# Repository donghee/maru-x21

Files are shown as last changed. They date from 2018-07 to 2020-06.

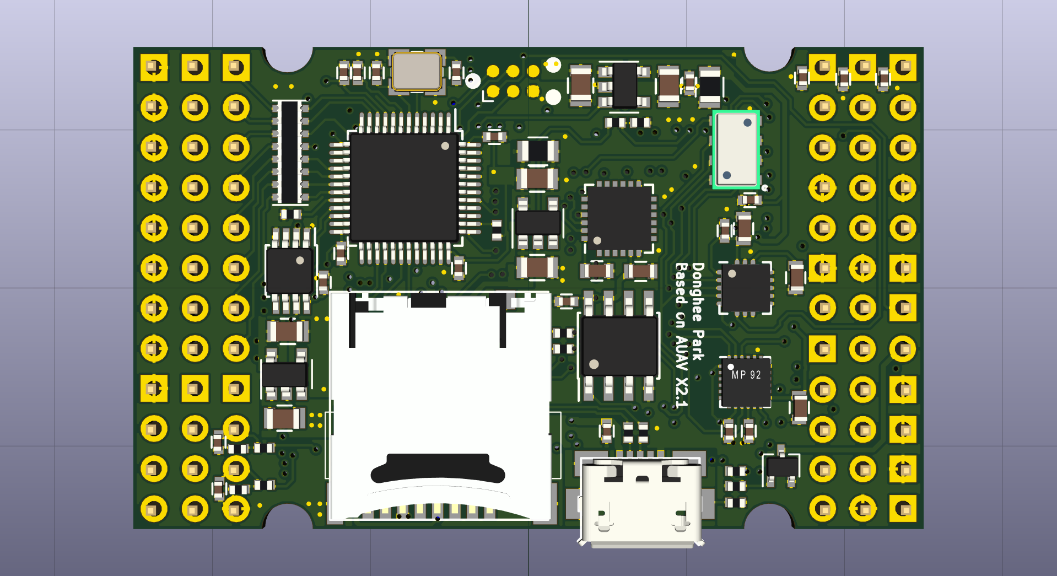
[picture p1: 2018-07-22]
maru-x21_3d_back.png

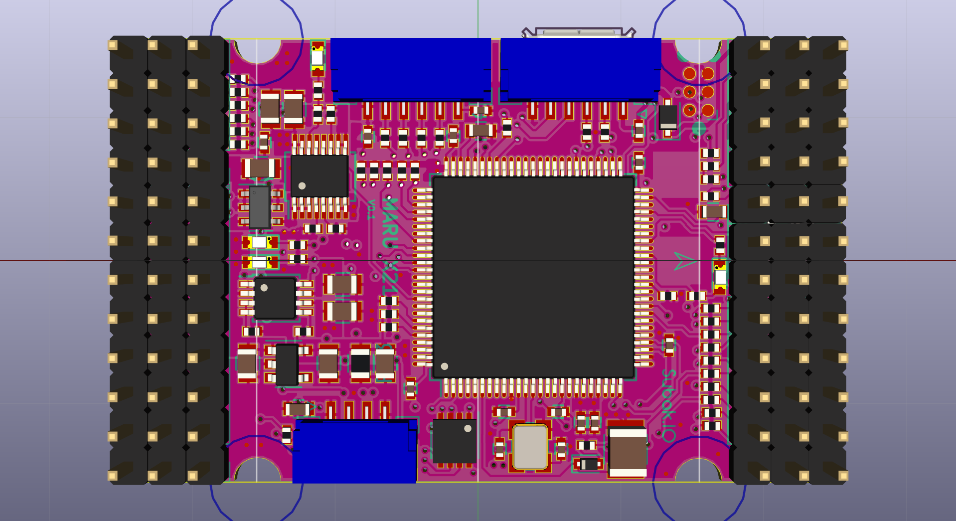
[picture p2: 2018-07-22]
maru-x21_3d_front.png

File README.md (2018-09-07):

# MARU X21

Pixhawk compatible autopilot based from AUAV X2.1

PCB assembly and program bootloader

PCB assembly (https://youtu.be/ogCYYdSt7_Y?t=0)

Case assembly

Case assembly (https://youtu.be/GHVFkq7RcLQ?t=0)

Maiden flight

Maiden flight (https://youtu.be/oDkj_PMFI5Y?t=0)

----

# Secification

FMU processor: stm32f427vit6
 - 32-bit ARM Cortex M4 core with FPU
 - 180 Mhz/256 KB RAM/2 MB Flash

IO processor: stm32f100c8t6
 - 32-bit ARM Cortex M3 core
 - 24 MHz/8 KB RAM/64 KB Flash

IMU sensors
 - icm-20602 6 axis accel and gyro (main imu)
 - mpu-9250 9 axis accel and gyro and mag
 - ms5611 barometer

Interfaces
 - 5x UARTs
 - 1x CANbus
 - RC Interfaces: PPM/SBUS/DSM/RSSI Input
 - I2C
 - SPI

Power Input
 - 4.8v~5.4v

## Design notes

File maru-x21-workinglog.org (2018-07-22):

* 사전조사

CUAV_Hardware

 - https://github.com/cuav/CUAV_Hardware/tree/master/6S_Smart%20batt-DEMO
 - https://github.com/cuav/CUAV_Hardware/tree/master/Pixhack_V3

Dropix

 - https://github.com/drotek/Dropix/blob/master/Hardware/Dropix.PDF

* Project Log

** <2017-12-31 일>
아침에 일어 났다. 'The Deveil is a Part-Timer'를 켜두고 pixracer
참고하는중. 

2017-12-31-13:58
목이 좀 아프네. 오늘의 목표 maru-pixracer-power 완성 

** <2018-02-04 일>

maru-pixracer 파워 패스 

PX4FMUv2 픽스호크는 servo 로부터 파워를 받는데 
X21_V2는 servo로 부터 파워를 받지 않는다. 
기본 파워는 VBUS(USB)와 V_BRICK(파워모듈)로 부터 받고 
LTC4415 (파워OR, 전류제한) 를 거쳐서 VDD_5V를 만든다. 
VDD_5V는 4개의 LDO(LP5907-Q1, 250mA)을 거쳐서 각각 
내부 파워 (IO_VDD_3V3, FMU_VDD_3V3, VDD_3V3_SPEKTRUM, VDD_3V3_SENSORS)로 출력되고 
VDD_5V는 TPS2062(1A Dual Current Limiter, 파워 스위치) 외부 파워에 나눌때는 TPS2062사용 를 거쳐 두개의 외부 파워 (VDD_5V_PERIPH, VDD_5V_RC)로 출력된다. 

** <2018-02-17 토>
 - [ ] schematic 그리기 작업 
201~200~FTSH-103-02-L-DV

** <2018-02-19 월>
maru 작업 순서 

 - 0. schematic 그리기
 - 1. schematic 검토 *
 - 2. part package 매칭
 - 3. pcb 그리기 
 - 4. 부품구매 
 - 5. 조립 
 - 6. 테스트/펌웨어 올리기

** <2018-02-21 화>
20mmx20mm 원점 잡고. maru x21 PCB 그리는중. 50x30.5 사이즈.

Dwgs.User에 가이드선 그리고 그리니깐 편리하네 

** <2018-02-22 Thu>

 - 3. pcb 그리기 작업중

FTSH-103-02-L-DV

** <2018-03-13 화>
 - 4층 각층은 동박은 1 ounce 두께로 주문 
 - 외곽선이 3지점 라인을 손상 시킨다. 한샘디지텍 외곽선 0.2 공차오차가
   있다. 그래서 좌우 0.5mm씩 늘려버리기로.
 주문한 메탈마스크 업체: 2장에 10만원 
 - 덕진전자 현수 010-5345-7023 dreammer70@hanmail.net
    경기도 광명시 광명로831번길 9, 3층 

** <2018-04-01 일>
 - 납땜 필요.
 -

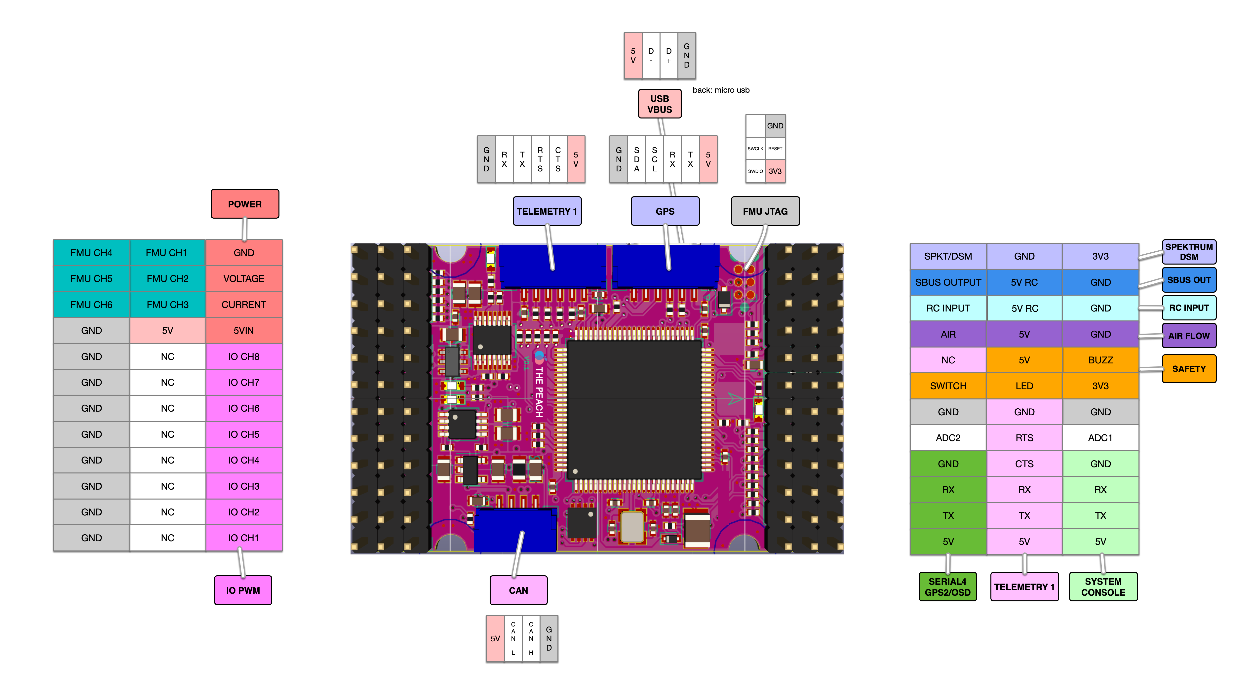
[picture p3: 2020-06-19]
doc/maru-x21-v01_legend.png

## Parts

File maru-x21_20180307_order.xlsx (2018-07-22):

C1-C7,C11,C20,C21,C28,C30-C36,C38-C41,C43,C49,C51,C52,C54,C57-C61 | 100nF | Capacitors_SMD:C_0402_NoSilk | GCM155R71C104KA55D | 32 | 45.4 | 1452.8 | 326637 | 45.4 | 1452.8 | 490-4759-1-ND
C10 | 220uF | Capacitors_SMD:C_1210 | CL32A227MQVNNNE | 1 | 1677 | 1677 | 309785 | 1677 | 1677 | 1276-3375-1-ND
C12,C13,C42,C48,C50 | 2u2F | Capacitors_SMD:C_0603 | C1608X5R1C225K080AB | 5 | 244 | 1220 | 302411 | 244 | 1220 | 445-5157-1-ND
C14-C17 | 2u2F 10V | Capacitors_SMD:C_0805 | C2012X5R1A225K085AA | 4 | 233 | 932 | 28286 | 233 | 932 | 445-1588-1-ND
C18,C19,C44,C45 | 8pF | Capacitors_SMD:C_0402_NoSilk | GRM1555C1E8R0CA01D | 4 | 116 | 464 | 48515 | 116 | 464 | 490-11372-1-ND
C22-C26 | 10uF 10V | Capacitors_SMD:C_0805 | C2012X5R1A106K085AB | 5 | 338 | 1690 | 142606 | 338 | 1690 | 445-7658-1-ND
C27,C29,C47 | 1uF | Capacitors_SMD:C_0603 | C1608X5R1C105K080AA | 3 | 116 | 348 | 17962 | 116 | 348 | 445-1416-1-ND
C46 | 470nF | Capacitors_SMD:C_0603 | GRM188R71C474KA88D | 1 | 198 | 198 | 459793 | 198 | 198 | 490-3295-1-ND
C53 | 10uF 16V | Capacitors_SMD:C_0805 | C2012X5R1C106K085AC | 1 | 303 | 303 | 57768 | 303 | 303 | 445-7644-1-ND
C55#2,C56#2 | 47uF 16V - p2/2 | Capacitors_SMD:C_0805 | LMK212BBJ476MG-T | 2 | 1106 | 2212 | 282 | 1106 | 2212 | 587-5465-1-ND
C8,C9 | 10uF 16V | Capacitors_SMD:C_0805 | C3216X5R1C106K160AA | 2 | 314 | 628 | 162965 | 314 | 628 | 445-4052-1-ND
D2#2 | BAS70-02V - p2/2 | Diodes_SMD:D_SOD-523 | BAS70KFILM | 1 | 303 | 303 | 31366 | 303 | 303 | 497-5695-1-ND
D6 | 1N4148WT | Diodes_SMD:D_SOD-523 | 1N4148WT | 1 | 233 | 233 | 243571 | 233 | 233 | 1N4148WTCT-ND
D7#1 | PMEG3002 - p1/2 | Diodes_SMD:D_SOD-323F | PMEG3002EJ | 1 | 594 | 594 | 74070 | 594 | 594 | 1727-5828-1-ND
J17 | SERIAL1 | Connectors_JST:JST_GH_SM06B-GHS-TB_06x1.25mm_Angled | SM06B-GHS-TB(LF)(SN) | 1 | 675 | 675 | 26740 | 675 | 675 | 455-1568-1-ND
J19 | CAN | Connectors_JST:JST_GH_SM04B-GHS-TB_04x1.25mm_Angled | SM04B-GHS-TB(LF)(SN)- | 1 | 524 | 524 | 84179 | 524 | 524 | 455-1566-1-ND
J22 | GPS/I2C | Connectors_JST:JST_GH_SM06B-GHS-TB_06x1.25mm_Angled | SM06B-GHS-TB(LF)(SN) | 1 | 675 | 675 | 26740 | 675 | 675 | 455-1568-1-ND
J4 | Micro_SD_Card | swi_sdcard:DM3CS-SF | DM3CS-SF | 1 | 1758 | 1758 | 20163 | 1758 | 1758 | HR1972CT-ND
P1 | USB_OTG | pkl_connectors:Connector_USB_Micro_B_SMD | 10118192-0001LF | 1 | 536 | 536 | 167623 | 536 | 536 | 609-4613-1-ND
Q1 | SI3493BDV | Housings_SSOP:TSOP-6_1.65x3.05mm_Pitch0.95mm | SI3493BDV-T1-E3 | 1 | 1013 | 1013 | 2716 | 1013 | 1013 | SI3493BDV-T1-E3CT-ND
Q2 | DMG1012UW | TO_SOT_Packages_SMD:SOT-323_SC-70 | DMG1012UW-7 | 1 | 454 | 454 | NonStk | 454 | 454 | DMG1012UW-7DICT-ND | element14
R1,R4,R34,R35,R38 | 470 | Resistors_SMD:R_0402_NoSilk | ERJ-2GEJ471X | 5 | 116 | 580 | 731945 | 116 | 580 | P470JCT-ND
R10,R11 | 470K | Resistors_SMD:R_0402_NoSilk | ERJ-2GEJ474X | 2 | 116 | 232 | 1980943 | 116 | 232 | P470KJCT-ND
R15,R29,R30 | 1K | Resistors_SMD:R_0402_NoSilk | ERJ-2GEJ102X | 3 | 116 | 348 | 969065 | 116 | 348 | P1.0KJCT-ND
R2,R8,R9,R12-R14,R33,R45,R46,R48-R52,R64 | 10K | Resistors_SMD:R_0402_NoSilk | RC1005J103CS | 15 | 14 | 210 | 317110 | 14 | 210 | 1276-4400-1-ND
R22,R23 | 220 | Resistors_SMD:R_0805 | RC2012J221CS | 2 | 116 | 232 | 91887 | 116 | 232 | 1276-5515-1-ND
R24 | 2K7 | Resistors_SMD:R_0402_NoSilk | ERJ-2GEJ272X | 1 | 116 | 116 | 351274 | 116 | 116 | P2.7KJCT-ND
R25,R26 | 1M | Resistors_SMD:R_0402_NoSilk | ERJ-2GEJ105X | 2 | 116 | 232 | 22059 | 116 | 232 | P1.0MJCT-ND
R27,R28 | 22 | Resistors_SMD:R_0402_NoSilk | ERJ-2GEJ220X | 2 | 116 | 232 | 3194228 | 116 | 232 | P22JCT-ND
R3,R7,R16-R20 | 100K | Resistors_SMD:R_0402_NoSilk | ERJ-2GEJ104X | 7 | 116 | 812 | 499925 | 116 | 812 | P100KJCT-ND
R31,R32,R39-R44,R53-R61,R65,R68-R73 | 220 | Resistors_SMD:R_0402_NoSilk | ERJ-2GEJ221X | 24 | 33.8 | 811.2 | 1861532 | 33.8 | 811.2 | P220JCT-ND
R36 | 47 | Resistors_SMD:R_0402_NoSilk | ERJ-2GEJ470X | 1 | 116 | 116 | 836865 | 116 | 116 | P47JCT-ND
R37,R66,R67 | 1K5 | Resistors_SMD:R_0402_NoSilk | ERJ-2GEJ152X | 3 | 116 | 348 | 1635661 | 116 | 348 | P1.5KJCT-ND
R47 | 10 | Resistors_SMD:R_0402_NoSilk | ERJ-2GEJ100X | 1 | 116 | 116 | 4075179 | 116 | 116 | P10JCT-ND
R5 | 200 1% | Resistors_SMD:R_0402_NoSilk | ERJ-2RKF2000X | 1 | 116 | 116 | 1402 | 116 | 116 | P200LCT-ND
R6 | 1K 1% | Resistors_SMD:R_0402_NoSilk | ERJ-2RKF1001X | 1 | 116 | 116 | 1120821 | 116 | 116 | P1.00KLCT-ND
R62 | 100 | Resistors_SMD:R_0402_NoSilk | ERJ-2GEJ101X | 1 | 116 | 116 | 1670945 | 116 | 116 | P100JCT-ND
R63 | 120 | Resistors_SMD:R_0402_NoSilk | ERJ-2GEJ121X | 1 | 116 | 116 | 624665 | 116 | 116 | P120JCT-ND
RN1 | 220 | Resistors_SMD:R_Cat16-8 | CAT16-221J8LF | 1 | 466 | 466 | 7585 | 466 | 466 | CAT16-221J8LFCT-ND
U1 | LTC4415 | Housings_SSOP:MSOP-16-1EP_3x4mm_Pitch0.5mm | LTC4415EMSE#PBF | 1 | 7463 | 7463 | 4642 | 7463 | 7463 | LTC4415EMSE#PBF-ND
U10 | MS5611-01BA03 | swi_sensors:ms5611-01ba03 | MS561101BA03-50 | 1 | 14530 | 14530 | NonStk | 14530 | 14530 | 223-1622-1-ND | element14
U11 | STM32F100C8T6 | Housings_QFP:LQFP-48_7x7mm_Pitch0.5mm | STM32F100C8T6B | 1 | 3854 | 3854 | 7195 | 3854 | 3854 | 497-10499-ND
U12 | ICM-20602 | swi_sensors:LGA-16_3x3mm_Pitch0.5mm | ICM-20602 | 1 | 6659 | 6659 | 17223 | 6659 | 6659 | 1428-1060-1-ND
U13#1 | TJA1051TK/3 - p1/2 | Housings_DFN_QFN:DFN-8-1EP_3x3mm_Pitch0.65mm | TJA1051TK/3 | 1 | 1234 | 1234 | 115301 | 1234 | 1234 | 568-8686-1-ND
U14#1 | 74LVC2G240 - p1/2 | Housings_SSOP:TSSOP-8_3x3mm_Pitch0.65mm | 74LVC2G240DP | 1 | 629 | 629 | 14869 | 629 | 629 | 1727-6678-1-ND
U15 | MPU-9250 | swi_sensors:QFN-24_3x3mm_Pitch0.4mm_large_pads | MPU-9250 | 1 | 12376 | 12376 | 56900 | 12376 | 12376 | 1428-1019-1-ND
U2 | TPS2062 | Housings_SSOP:MSOP-8-1EP_3x3mm_Pitch0.65mm | TPS2062CDGNR | 1 | 2177 | 2177 | 1345 | 2177 | 2177 | 296-41720-1-ND
U3 | STM32F427VIT6 | Housings_QFP:LQFP-100_14x14mm_Pitch0.5mm | STM32F427VIT6 | 1 | 16707 | 16707 | NonStk | 16707 | 16707 | 497-14049-ND | element14
U4-U7 | LP5907 | TO_SOT_Packages_SMD:SOT-23-5 | LP5907QMFX-3.3Q1 | 4 | 757 | 3028 | 21427 | 757 | 3028 | 296-40365-1-ND
U8 | FM25V02A-G | Housings_SOIC:SOIC-8_3.9x4.9mm_Pitch1.27mm | FM25V02A-G | 1 | 8150 | 8150 | 9435 | 8150 | 8150 | 428-3386-ND
X1,X2 | 24MHz | swi_misc:ABM8 | NX3225SA-24.000MHZ-STD-CSR-1 | 2 | 873 | 1746 | 49910 | 873 | 1746 | 644-1052-1-ND
부품종류
51 | 가지

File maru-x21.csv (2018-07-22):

Source: | /Users/donghee/Dropbox/dev/electrical/kicad/maru/maru-pixracer/maru-pixracer.sch
Date: | 2018 March 14, Wednesday 18:42:59
Tool: | Eeschema 4.0.7
Generator: | /Applications/Kicad/kicad.app/Contents/SharedSupport/plugins/bom_csv_grouped_by_value.py
Component Count: | 188
Individual Components:
Item | Qty | Reference(s) | Value | LibPart | Footprint | Datasheet | #mouser | digikey# | manf#
 |  | C1 | 100nF | maru-pixracer-cache:C_Small | swi_dipol:C_0402 |  |  |  | GCM155R71C104KA55D
 |  | C2 | 100nF | maru-pixracer-cache:C_Small | swi_dipol:C_0402 |  |  |  | GCM155R71C104KA55D
 |  | C3 | 100nF | maru-pixracer-cache:C_Small | swi_dipol:C_0402 |  |  |  | GCM155R71C104KA55D
 |  | C4 | 100nF | maru-pixracer-cache:C_Small | swi_dipol:C_0402 |  |  |  | GCM155R71C104KA55D
 |  | C5 | 100nF | maru-pixracer-cache:C_Small | swi_dipol:C_0402 |  |  |  | GCM155R71C104KA55D
 |  | C6 | 100nF | maru-pixracer-cache:C_Small | swi_dipol:C_0402 |  |  |  | GCM155R71C104KA55D
 |  | C7 | 100nF | maru-pixracer-cache:C_Small | swi_dipol:C_0402 |  |  |  | GCM155R71C104KA55D
 |  | C8 | 10uF 16V | maru-pixracer-cache:C_Small | swi_dipol:C_0805 |  |  |  | C3216X5R1C106K160AA
 |  | C9 | 10uF 16V | maru-pixracer-cache:C_Small | swi_dipol:C_0805 |  |  |  | C3216X5R1C106K160AA
 |  | C10 | 220uF | maru-pixracer-cache:C_Small | Capacitors_SMD:C_1210 |  |  |  | CL32A227MQVNNNE
 |  | C11 | 100nF | maru-pixracer-cache:C_Small | swi_dipol:C_0402 |  |  |  | GCM155R71C104KA55D
 |  | C12 | 2u2F | maru-pixracer-cache:C_Small | swi_dipol:C_0603 |  |  |  | C1608X5R1C225K080AB
 |  | C13 | 2u2F | maru-pixracer-cache:C_Small | swi_dipol:C_0603 |  |  |  | C1608X5R1C225K080AB
 |  | C14 | 2u2F 10V | maru-pixracer-cache:C_Small | swi_dipol:C_0805 |  |  |  | C2012X5R1A225K085AA
 |  | C15 | 2u2F 10V | maru-pixracer-cache:C_Small | swi_dipol:C_0805 |  |  |  | C2012X5R1A225K085AA
 |  | C16 | 2u2F 10V | maru-pixracer-cache:C_Small | swi_dipol:C_0805 |  |  |  | C2012X5R1A225K085AA
 |  | C17 | 2u2F 10V | maru-pixracer-cache:C_Small | swi_dipol:C_0805 |  |  |  | C2012X5R1A225K085AA
 |  | C18 | 8pF | maru-pixracer-cache:C_Small | swi_dipol:C_0402 |  |  |  | GRM1555C1E8R0CA01D
 |  | C19 | 8pF | maru-pixracer-cache:C_Small | swi_dipol:C_0402 |  |  |  | GRM1555C1E8R0CA01D
 |  | C20 | 100nF | maru-pixracer-cache:C_Small | swi_dipol:C_0402 |  |  |  | GCM155R71C104KA55D
 |  | C21 | 100nF | maru-pixracer-cache:C_Small | swi_dipol:C_0402 |  |  |  | GCM155R71C104KA55D
 |  | C22 | 10uF 10V | maru-pixracer-cache:C_Small | swi_dipol:C_0805 |  |  |  | C2012X5R1A106K085AB
 |  | C23 | 10uF 10V | maru-pixracer-cache:C_Small | swi_dipol:C_0805 |  |  |  | C2012X5R1A106K085AB
 |  | C24 | 10uF 10V | maru-pixracer-cache:C_Small | swi_dipol:C_0805 |  |  |  | C2012X5R1A106K085AB
 |  | C25 | 10uF 10V | maru-pixracer-cache:C_Small | swi_dipol:C_0805 |  |  |  | C2012X5R1A106K085AB
 |  | C26 | 10uF 10V | maru-pixracer-cache:C_Small | swi_dipol:C_0805 |  |  |  | C2012X5R1A106K085AB
 |  | C27 | 1uF | maru-pixracer-cache:C_Small | swi_dipol:C_0603 |  |  |  | C1608X5R1C105K080AA
 |  | C28 | 100nF | maru-pixracer-cache:C_Small | swi_dipol:C_0402 |  |  |  | GCM155R71C104KA55D
 |  | C29 | 1uF | maru-pixracer-cache:C_Small | swi_dipol:C_0603 |  |  |  | C1608X5R1C105K080AA
 |  | C30 | 100nF | maru-pixracer-cache:C_Small | swi_dipol:C_0402 |  |  |  | GCM155R71C104KA55D
 |  | C31 | 100nF | maru-pixracer-cache:C_Small | swi_dipol:C_0402 |  |  |  | GCM155R71C104KA55D
 |  | C32 | 100nF | maru-pixracer-cache:C_Small | swi_dipol:C_0402 |  |  |  | GCM155R71C104KA55D
 |  | C33 | 100nF | maru-pixracer-cache:C_Small | swi_dipol:C_0402 |  |  |  | GCM155R71C104KA55D
 |  | C34 | 100nF | maru-pixracer-cache:C_Small | swi_dipol:C_0402 |  |  |  | GCM155R71C104KA55D
 |  | C35 | 100nF | maru-pixracer-cache:C_Small | swi_dipol:C_0402 |  |  |  | GCM155R71C104KA55D
 |  | C36 | 100nF | maru-pixracer-cache:C_Small | swi_dipol:C_0402 |  |  |  | GCM155R71C104KA55D
 |  | C38 | 100nF | maru-pixracer-cache:C_Small | swi_dipol:C_0402 |  |  |  | GCM155R71C104KA55D
 |  | C39 | 100nF | maru-pixracer-cache:C_Small | swi_dipol:C_0402 |  |  |  | GCM155R71C104KA55D
 |  | C40 | 100nF | maru-pixracer-cache:C_Small | swi_dipol:C_0402 |  |  |  | GCM155R71C104KA55D
 |  | C41 | 100nF | maru-pixracer-cache:C_Small | swi_dipol:C_0402 |  |  |  | GCM155R71C104KA55D
 |  | C42 | 2u2F | maru-pixracer-cache:C_Small | swi_dipol:C_0603 |  |  |  | C1608X5R1C225K080AB
 |  | C43 | 100nF | maru-pixracer-cache:C_Small | swi_dipol:C_0402 |  |  |  | GCM155R71C104KA55D
 |  | C44 | 8pF | maru-pixracer-cache:C_Small | swi_dipol:C_0402 |  |  |  | GRM1555C1E8R0CA01D
 |  | C45 | 8pF | maru-pixracer-cache:C_Small | swi_dipol:C_0402 |  |  |  | GRM1555C1E8R0CA01D
 |  | C46 | 470nF | maru-pixracer-cache:C_Small | swi_dipol:C_0603 |  |  |  | GRM188R71C474KA88D
 |  | C47 | 1uF | maru-pixracer-cache:C_Small | swi_dipol:C_0603 |  |  |  | C1608X5R1C105K080AA
 |  | C48 | 2u2F | maru-pixracer-cache:C_Small | swi_dipol:C_0603 |  |  |  | C1608X5R1C225K080AB
 |  | C49 | 100nF | maru-pixracer-cache:C_Small | swi_dipol:C_0402 |  |  |  | GCM155R71C104KA55D
 |  | C50 | 2u2F | maru-pixracer-cache:C_Small | swi_dipol:C_0603 |  |  |  | C1608X5R1C225K080AB
 |  | C51 | 100nF | maru-pixracer-cache:C_Small | swi_dipol:C_0402 |  |  |  | GCM155R71C104KA55D
 |  | C52 | 100nF | maru-pixracer-cache:C_Small | swi_dipol:C_0402 |  |  |  | GCM155R71C104KA55D
 |  | C53 | 10uF 16V | maru-pixracer-cache:C_Small | swi_dipol:C_0805 |  |  |  | C2012X5R1C106K085AC
 |  | C54 | 100nF | maru-pixracer-cache:C_Small | swi_dipol:C_0402 |  |  |  | GCM155R71C104KA55D
 |  | C55 | 47uF 16V | maru-pixracer-cache:C_Small | swi_dipol:C_0805 |  |  |  | C2012X5R1A476M125AC, LMK212BBJ476MG-T
 |  | C56 | 47uF 16V | maru-pixracer-cache:C_Small | swi_dipol:C_0805 |  |  |  | C2012X5R1A476M125AC, LMK212BBJ476MG-T
 |  | C57 | 100nF | maru-pixracer-cache:C_Small | swi_dipol:C_0402 |  |  |  | GCM155R71C104KA55D
 |  | C58 | 100nF | maru-pixracer-cache:C_Small | swi_dipol:C_0402 |  |  |  | GCM155R71C104KA55D
 |  | C59 | 100nF | maru-pixracer-cache:C_Small | swi_dipol:C_0402 |  |  |  | GCM155R71C104KA55D
 |  | C60 | 100nF | maru-pixracer-cache:C_Small | swi_dipol:C_0402 |  |  |  | GCM155R71C104KA55D
 |  | C61 | 100nF | maru-pixracer-cache:C_Small | swi_dipol:C_0402 |  |  |  | GCM155R71C104KA55D
 |  | D1 | RED | maru-pixracer-cache:LED | LEDs:LED_0603
 |  | D2 | BAS70-02V | maru-pixracer-cache:D_Schottky | Diodes_SMD:D_SOD-523 |  |  |  | BAS70-02V-V-G-08, BAS70KFILM
 |  | D3 | GREEN | maru-pixracer-cache:LED | LEDs:LED_0603
 |  | D4 | RED | maru-pixracer-cache:LED | LEDs:LED_0603
 |  | D5 | BLUE | maru-pixracer-cache:LED | LEDs:LED_0603
 |  | D6 | 1N4148WT | maru-pixracer-cache:D_Schottky_Small | Diodes_SMD:D_SOD-523 |  |  |  | 1N4148WT
 |  | D7 | PMEG3002 | maru-pixracer-cache:D_Schottky | Diodes_SMD:D_SOD-323F |  |  |  | PMEG3002EJ,115
 |  | J1 | ARM Cortex JTAG 6p | maru-pixracer-cache:Conn_02x03_Odd_Even | swi_pads:Tag-Connect_TC2030-IDC-NL-NOHOLE
 |  | J2 | ARM Cortex JTAG 6p | maru-pixracer-cache:Conn_02x03_Odd_Even | swi_pads:Tag-Connect_TC2030-IDC-NL-NOHOLE
 |  | J3 | BRICK | maru-pixracer-cache:Conn_01x04 | Pin_Headers:Pin_Header_Straight_1x04_Pitch2.54mm
 |  | J4 | Micro_SD_Card | maru-pixracer-cache:Micro_SD_Card | swi_sdcard:DM3CS-SF |  |  |  | DM3CS-SF
 |  | J5 | IO_CHANNELS | maru-pixracer-cache:Conn_01x08 | Pin_Headers:Pin_Header_Straight_1x08_Pitch2.54mm
 |  | J6 | VDD_SERVO | maru-pixracer-cache:Conn_01x08 | Pin_Headers:Pin_Header_Straight_1x08_Pitch2.54mm
 |  | J7 | SERVO_GND | maru-pixracer-cache:Conn_01x08 | Pin_Headers:Pin_Header_Straight_1x08_Pitch2.54mm
 |  | J8 | SAFETY | maru-pixracer-cache:Conn_01x03 | Pin_Headers:Pin_Header_Straight_1x03_Pitch2.54mm
 |  | J9 | CH1-3 | maru-pixracer-cache:Conn_01x04 | Pin_Headers:Pin_Header_Straight_1x04_Pitch2.54mm
 |  | J10 | CH4-6 | maru-pixracer-cache:Conn_01x04 | Pin_Headers:Pin_Header_Straight_1x04_Pitch2.54mm
 |  | J11 | BUZZ | maru-pixracer-cache:Conn_01x03 | Pin_Headers:Pin_Header_Straight_1x03_Pitch2.54mm
 |  | J12 | AIR | maru-pixracer-cache:Conn_01x03 | Pin_Headers:Pin_Header_Straight_1x03_Pitch2.54mm
 |  | J13 | AUX-ADC1 | maru-pixracer-cache:Conn_01x02 | Pin_Headers:Pin_Header_Straight_1x02_Pitch2.54mm
 |  | J14 | AUX-ADC2 | maru-pixracer-cache:Conn_01x02 | Pin_Headers:Pin_Header_Straight_1x02_Pitch2.54mm
 |  | J15 | SIPI | maru-pixracer-cache:Conn_01x03 | Pin_Headers:Pin_Header_Straight_1x03_Pitch2.54mm
 |  | J16 | SPEKT | maru-pixracer-cache:Conn_01x03 | Pin_Headers:Pin_Header_Straight_1x03_Pitch2.54mm
 |  | J17 | SERIAL1 | maru-pixracer-cache:Conn_01x06 | Connectors_JST:JST_GH_SM06B-GHS-TB_06x1.25mm_Angled |  |  |  | SM06B-GHS-TB(LF)(SN)
 |  | J18 | TELEM2 | maru-pixracer-cache:Conn_01x06 | Pin_Headers:Pin_Header_Straight_1x06_Pitch2.54mm
 |  | J19 | CAN | maru-pixracer-cache:Conn_01x04 | Connectors_JST:JST_GH_SM04B-GHS-TB_04x1.25mm_Angled |  |  |  | SM04B-GHS-TB(LF)(SN)-
 |  | J20 | SERIAL4 | maru-pixracer-cache:Conn_01x04 | Pin_Headers:Pin_Header_Straight_1x04_Pitch2.54mm
 |  | J21 | SERIAL5 | maru-pixracer-cache:Conn_01x04 | Pin_Headers:Pin_Header_Straight_1x04_Pitch2.54mm
 |  | J22 | GPS/I2C | maru-pixracer-cache:Conn_01x06 | Connectors_JST:JST_GH_SM06B-GHS-TB_06x1.25mm_Angled |  |  |  | SM06B-GHS-TB(LF)(SN)
 |  | J23 | SORI | maru-pixracer-cache:Conn_01x03 | Pin_Headers:Pin_Header_Straight_1x03_Pitch2.54mm
 |  | LOGO1 | OPEN_HARDWARE_1 | maru-pixracer-cache:OPEN_HARDWARE_1 | Symbols:OSHW-Logo_5.7x6mm_SilkScreen
 |  | M1 | MOUNTING-HOLE | maru-pixracer-cache:MOUNTING-HOLE | Mounting_Holes:MountingHole_3.2mm_M3
 |  | M2 | MOUNTING-HOLE | maru-pixracer-cache:MOUNTING-HOLE | Mounting_Holes:MountingHole_3.2mm_M3
 |  | M3 | MOUNTING-HOLE | maru-pixracer-cache:MOUNTING-HOLE | Mounting_Holes:MountingHole_3.2mm_M3
 |  | M4 | MOUNTING-HOLE | maru-pixracer-cache:MOUNTING-HOLE | Mounting_Holes:MountingHole_3.2mm_M3
 |  | P1 | USB_OTG | maru-pixracer-cache:pkl_USB_OTG | pkl_connectors:Connector_USB_Micro_B_SMD |  |  |  | 10118192-0001LF
 |  | Q1 | SI3493BDV | maru-pixracer-cache:SI3493BDV | Housings_SSOP:TSOP-6_1.65x3.05mm_Pitch0.95mm | https://www.vishay.com/docs/74478/si3493bdv.pdf |  |  | SI3493BDV-T1-E3
 |  | Q2 | DMG1012UW | maru-pixracer-cache:2N7002 | TO_SOT_Packages_SMD:SOT-323_SC-70 |  | 621-DMG1012UW-7 |  | DMG1012UW-7
 |  | R1 | 470 | maru-pixracer-cache:R_Small | swi_dipol:R_0402_NoSilk |  |  |  | ERJ-2GEJ471X
 |  | R2 | 10K | maru-pixracer-cache:R_Small | swi_dipol:R_0402_NoSilk |  |  |  | RC1005J103CS
 |  | R4 | 470 | maru-pixracer-cache:R_Small | swi_dipol:R_0402_NoSilk |  |  |  | ERJ-2GEJ471X
 |  | R5 | 200 1% | maru-pixracer-cache:R_Small | swi_dipol:R_0402_NoSilk | https://industrial.panasonic.com/cdbs/www-data/pdf/RDA0000/AOA0000C304.pdf |  |  | ERJ-2RKF2000X
 |  | R6 | 1K 1% | maru-pixracer-cache:R_Small | swi_dipol:R_0402_NoSilk |  |  |  | ERJ-2RKF1001X
 |  | R7 | 100K | maru-pixracer-cache:R_Small | swi_dipol:R_0402_NoSilk |  |  |  | ERJ-2GEJ104X
 |  | R8 | 10K | maru-pixracer-cache:R_Small | swi_dipol:R_0402_NoSilk |  |  |  | RC1005J103CS
 |  | R9 | 10K | maru-pixracer-cache:R_Small | swi_dipol:R_0402_NoSilk |  |  |  | RC1005J103CS
 |  | R10 | 470K | maru-pixracer-cache:R_Small | swi_dipol:R_0402_NoSilk |  |  |  | ERJ-2GEJ474X
 |  | R11 | 470K | maru-pixracer-cache:R_Small | swi_dipol:R_0402_NoSilk |  |  |  | ERJ-2GEJ474X
 |  | R12 | 10K | maru-pixracer-cache:R_Small | swi_dipol:R_0402_NoSilk |  |  |  | RC1005J103CS
 |  | R13 | 10K | maru-pixracer-cache:R_Small | swi_dipol:R_0402_NoSilk |  |  |  | RC1005J103CS
 |  | R14 | 10K | maru-pixracer-cache:R_Small | swi_dipol:R_0402_NoSilk |  |  |  | RC1005J103CS
 |  | R15 | 1K | maru-pixracer-cache:R_Small | swi_dipol:R_0402_NoSilk |  |  |  | ERJ-2GEJ102X
 |  | R16 | 100K | maru-pixracer-cache:R_Small | swi_dipol:R_0402_NoSilk |  |  |  | ERJ-2GEJ104X
 |  | R17 | 100K | maru-pixracer-cache:R_Small | swi_dipol:R_0402_NoSilk |  |  |  | ERJ-2GEJ104X
 |  | R18 | 100K | maru-pixracer-cache:R_Small | swi_dipol:R_0402_NoSilk |  |  |  | ERJ-2GEJ104X
 |  | R19 | 100K | maru-pixracer-cache:R_Small | swi_dipol:R_0402_NoSilk |  |  |  | ERJ-2GEJ104X
 |  | R20 | 100K | maru-pixracer-cache:R_Small | swi_dipol:R_0402_NoSilk |  |  |  | ERJ-2GEJ104X
 |  | R21 | DNP | maru-pixracer-cache:R_Small | swi_dipol:R_0805 |  |  |  | -
 |  | R22 | 220 | maru-pixracer-cache:R_Small | swi_dipol:R_0805 |  |  |  | RC2012J221CS
 |  | R23 | 220 | maru-pixracer-cache:R_Small | swi_dipol:R_0805 |  |  |  | RC2012J221CS
 |  | R24 | 2K7 | maru-pixracer-cache:R_Small | swi_dipol:R_0402_NoSilk |  |  |  | ERJ-2GEJ272X
 |  | R25 | 1M | maru-pixracer-cache:R_Small | swi_dipol:R_0402_NoSilk |  |  |  | ERJ-2GEJ105X
 |  | R26 | 1M | maru-pixracer-cache:R_Small | swi_dipol:R_0402_NoSilk |  |  |  | ERJ-2GEJ105X
 |  | R27 | 22 | maru-pixracer-cache:R_Small | swi_dipol:R_0402_NoSilk |  |  |  | ERJ-2GEJ220X
 |  | R28 | 22 | maru-pixracer-cache:R_Small | swi_dipol:R_0402_NoSilk |  |  |  | ERJ-2GEJ220X
 |  | R29 | 1K | maru-pixracer-cache:R_Small | swi_dipol:R_0402_NoSilk |  |  |  | ERJ-2GEJ102X
 |  | R30 | 1K | maru-pixracer-cache:R_Small | swi_dipol:R_0402_NoSilk |  |  |  | ERJ-2GEJ102X
 |  | R31 | 220 | maru-pixracer-cache:R_Small | swi_dipol:R_0402_NoSilk |  |  |  | ERJ-2GEJ221X
 |  | R32 | 220 | maru-pixracer-cache:R_Small | swi_dipol:R_0402_NoSilk |  |  |  | ERJ-2GEJ221X
 |  | R33 | 10K | maru-pixracer-cache:R_Small | swi_dipol:R_0402_NoSilk |  |  |  | RC1005J103CS
 |  | R34 | 470 | maru-pixracer-cache:R_Small | swi_dipol:R_0402_NoSilk |  |  |  | ERJ-2GEJ471X
 |  | R35 | 470 | maru-pixracer-cache:R_Small | swi_dipol:R_0402_NoSilk |  |  |  | ERJ-2GEJ471X
 |  | R36 | 47 | maru-pixracer-cache:R_Small | swi_dipol:R_0402_NoSilk |  |  |  | ERJ-2GEJ470X
 |  | R37 | 1K5 | maru-pixracer-cache:R_Small | swi_dipol:R_0402_NoSilk |  |  |  | ERJ-2GEJ152X
 |  | R38 | 470 | maru-pixracer-cache:R_Small | swi_dipol:R_0402_NoSilk |  |  |  | ERJ-2GEJ471X
 |  | R39 | 220 | maru-pixracer-cache:R_Small | swi_dipol:R_0402_NoSilk |  |  |  | ERJ-2GEJ221X
 |  | R40 | 220 | maru-pixracer-cache:R_Small | swi_dipol:R_0402_NoSilk |  |  |  | ERJ-2GEJ221X
 |  | R41 | 220 | maru-pixracer-cache:R_Small | swi_dipol:R_0402_NoSilk |  |  |  | ERJ-2GEJ221X
 |  | R42 | 220 | maru-pixracer-cache:R_Small | swi_dipol:R_0402_NoSilk |  |  |  | ERJ-2GEJ221X
 |  | R43 | 220 | maru-pixracer-cache:R_Small | swi_dipol:R_0402_NoSilk |  |  |  | ERJ-2GEJ221X
 |  | R44 | 220 | maru-pixracer-cache:R_Small | swi_dipol:R_0402_NoSilk |  |  |  | ERJ-2GEJ221X
 |  | R45 | 10K | maru-pixracer-cache:R_Small | swi_dipol:R_0402_NoSilk |  |  |  | RC1005J103CS
 |  | R46 | 10K | maru-pixracer-cache:R_Small | swi_dipol:R_0402_NoSilk |  |  |  | RC1005J103CS
 |  | R47 | 10 | maru-pixracer-cache:R_Small | swi_dipol:R_0402_NoSilk |  |  |  | ERJ-2GEJ100X
 |  | R48 | 10K | maru-pixracer-cache:R_Small | swi_dipol:R_0402_NoSilk |  |  |  | RC1005J103CS
 |  | R49 | 10K | maru-pixracer-cache:R_Small | swi_dipol:R_0402_NoSilk |  |  |  | RC1005J103CS
 |  | R50 | 10K | maru-pixracer-cache:R_Small | swi_dipol:R_0402_NoSilk |  |  |  | RC1005J103CS
 |  | R51 | 10K | maru-pixracer-cache:R_Small | swi_dipol:R_0402_NoSilk |  |  |  | RC1005J103CS
 |  | R52 | 10K | maru-pixracer-cache:R_Small | swi_dipol:R_0402_NoSilk |  |  |  | RC1005J103CS
 |  | R53 | 220 | maru-pixracer-cache:R_Small | swi_dipol:R_0402_NoSilk |  |  |  | ERJ-2GEJ221X
 |  | R54 | 220 | maru-pixracer-cache:R_Small | swi_dipol:R_0402_NoSilk |  |  |  | ERJ-2GEJ221X
 |  | R55 | 220 | maru-pixracer-cache:R_Small | swi_dipol:R_0402_NoSilk |  |  |  | ERJ-2GEJ221X
 |  | R56 | 220 | maru-pixracer-cache:R_Small | swi_dipol:R_0402_NoSilk |  |  |  | ERJ-2GEJ221X
 |  | R57 | 220 | maru-pixracer-cache:R_Small | swi_dipol:R_0402_NoSilk |  |  |  | ERJ-2GEJ221X
 |  | R58 | 220 | maru-pixracer-cache:R_Small | swi_dipol:R_0402_NoSilk |  |  |  | ERJ-2GEJ221X
 |  | R59 | 220 | maru-pixracer-cache:R_Small | swi_dipol:R_0402_NoSilk |  |  |  | ERJ-2GEJ221X
 |  | R60 | 220 | maru-pixracer-cache:R_Small | swi_dipol:R_0402_NoSilk |  |  |  | ERJ-2GEJ221X
 |  | R61 | 220 | maru-pixracer-cache:R_Small | swi_dipol:R_0402_NoSilk |  |  |  | ERJ-2GEJ221X
 |  | R62 | 100 | maru-pixracer-cache:R_Small | swi_dipol:R_0402_NoSilk |  |  |  | ERJ-2GEJ101X
 |  | R63 | 120 | maru-pixracer-cache:R | swi_dipol:R_0402_NoSilk |  |  |  | ERJ-2GEJ121X
 |  | R64 | 10K | maru-pixracer-cache:R_Small | swi_dipol:R_0402_NoSilk |  |  |  | RC1005J103CS
 |  | R65 | 220 | maru-pixracer-cache:R_Small | swi_dipol:R_0402_NoSilk |  |  |  | ERJ-2GEJ221X
 |  | R66 | 1K5 | maru-pixracer-cache:R_Small | swi_dipol:R_0402_NoSilk |  |  |  | ERJ-2GEJ152X
 |  | R67 | 1K5 | maru-pixracer-cache:R_Small | swi_dipol:R_0402_NoSilk |  |  |  | ERJ-2GEJ152X
 |  | R68 | 220 | maru-pixracer-cache:R_Small | swi_dipol:R_0402_NoSilk |  |  |  | ERJ-2GEJ221X
 |  | R69 | 220 | maru-pixracer-cache:R_Small | swi_dipol:R_0402_NoSilk |  |  |  | ERJ-2GEJ221X
 |  | R70 | 220 | maru-pixracer-cache:R_Small | swi_dipol:R_0402_NoSilk |  |  |  | ERJ-2GEJ221X
 |  | R71 | 220 | maru-pixracer-cache:R_Small | swi_dipol:R_0402_NoSilk |  |  |  | ERJ-2GEJ221X
 |  | R72 | 220 | maru-pixracer-cache:R_Small | swi_dipol:R_0402_NoSilk |  |  |  | ERJ-2GEJ221X
 |  | R73 | 220 | maru-pixracer-cache:R_Small | swi_dipol:R_0402_NoSilk |  |  |  | ERJ-2GEJ221X
 |  | RN1 | 220 | maru-pixracer-cache:R_Pack08 | Resistors_SMD:R_Cat16-8 | http://www.bourns.com/docs/Product-Datasheets/CATCAY.pdf |  |  | CAT16-221J8LF
 |  | U1 | LTC4415 | maru-pixracer-cache:LTC4415 | Housings_SSOP:MSOP-16-1EP_3x4mm_Pitch0.5mm | http://cds.linear.com/docs/en/datasheet/4415fa.pdf |  |  | LTC4415EMSE#PBF
 |  | U2 | TPS2062 | maru-pixracer-cache:TPS2062 | Housings_SSOP:MSOP-8-1EP_3x3mm_Pitch0.65mm | http://www.ti.com/lit/ds/symlink/tps2062c.pdf |  |  | TPS2062CDGNR
 |  | U3 | STM32F427VIT6 | maru-pixracer-cache:STM32F427VIT6 | swi_housings_qfp:LQFP-100-L_14x14mm_Pitch0.5mm |  |  |  | STM32F427VIT6
 |  | U4 | LP5907 | maru-pixracer-cache:LP5907 | TO_SOT_Packages_SMD:SOT-23-5 | http://www.ti.com/lit/ds/symlink/lp5907.pdf |  |  | LP5907QMFX-3.3Q1
 |  | U5 | LP5907 | maru-pixracer-cache:LP5907 | TO_SOT_Packages_SMD:SOT-23-5 | http://www.ti.com/lit/ds/symlink/lp5907.pdf |  |  | LP5907QMFX-3.3Q1
 |  | U6 | LP5907 | maru-pixracer-cache:LP5907 | TO_SOT_Packages_SMD:SOT-23-5 | http://www.ti.com/lit/ds/symlink/lp5907.pdf |  |  | LP5907QMFX-3.3Q1
 |  | U7 | LP5907 | maru-pixracer-cache:LP5907 | TO_SOT_Packages_SMD:SOT-23-5 | http://www.ti.com/lit/ds/symlink/lp5907.pdf |  |  | LP5907QMFX-3.3Q1
 |  | U8 | FM25V02A-G | maru-pixracer-cache:M25P16-VME | Housings_SOIC:SOIC-8_3.9x4.9mm_Pitch1.27mm |  |  |  | FM25V02A-G
 |  | U9 | DORCA30 | maru-pixracer-cache:DORCA30 | swi_housings_qfp:QFN-24_4x4mm_Pitch0.5mm
 |  | U10 | MS5611-01BA03 | maru-pixracer-cache:MS5611-01BA03 | swi_sensors:ms5611-01ba03 |  |  |  | MS561101BA03-50
 |  | U11 | STM32F100C8T6 | maru-pixracer-cache:STM32F100C8T6 | swi_housings_qfp:LQFP-48-L_7x7mm_Pitch0.5mm |  |  |  | STM32F100C8T6B
 |  | U12 | ICM-20602 | maru-pixracer-cache:ICM-20602 | swi_sensors:LGA-16_3x3mm_Pitch0.5mm | https://www.invensense.com/wp-content/uploads/2015/12/ICM-20602-Product-Brief-v1.0.pdf |  | 1428-1060-1-ND | ICM-20602
 |  | U13 | TJA1051TK/3 | maru-pixracer-cache:TJA1051TK/3 | Housings_DFN_QFN:DFN-8-1EP_3x3mm_Pitch0.65mm |  |  | 568-8686-1-ND | TJA1051TK/3,118
 |  | U14 | 74LVC2G240 | maru-pixracer-cache:74LVC2G240 | Housings_SSOP:TSSOP-8_3x3mm_Pitch0.65mm |  |  |  | 74LVC2G240DP,125
 |  | U15 | MPU-9250 | maru-pixracer-cache:MPU-9250 | swi_sensors:QFN-24_3x3mm_Pitch0.4mm_large_pads |  |  | 1428-1019-1-ND | MPU-9250
 |  | X1 | 24MHz | maru-pixracer-cache:swi_XTAL_XGXG | swi_misc:ABM8 |  |  |  | NX3225SA-24.000MHZ-STD-CSR-1
 |  | X2 | 24MHz | maru-pixracer-cache:swi_XTAL_XGXG | swi_misc:ABM8 |  |  |  | NX3225SA-24.000MHZ-STD-CSR-1
Collated Components:
Item | Qty | Reference(s) | Value | LibPart | Footprint | Datasheet | #mouser | digikey# | manf#
1 | 32 | C1, C2, C3, C4, C5, C6, C7, C11, C20, C21, C28, C30, C31, C32, C33, C34, C35, C36, C38, C39, C40, C41, C43, C49, C51, C52, C54, C57, C58, C59, C60, C61 | 100nF | maru-pixracer-cache:C_Small | swi_dipol:C_0402 |  |  |  | GCM155R71C104KA55D
2 | 3 | C8, C9, C53 | 10uF 16V | maru-pixracer-cache:C_Small | swi_dipol:C_0805 |  |  |  | C3216X5R1C106K160AA
3 | 1 | C10 | 220uF | maru-pixracer-cache:C_Small | Capacitors_SMD:C_1210 |  |  |  | CL32A227MQVNNNE
4 | 5 | C12, C13, C42, C48, C50 | 2u2F | maru-pixracer-cache:C_Small | swi_dipol:C_0603 |  |  |  | C1608X5R1C225K080AB
5 | 4 | C14, C15, C16, C17 | 2u2F 10V | maru-pixracer-cache:C_Small | swi_dipol:C_0805 |  |  |  | C2012X5R1A225K085AA
6 | 4 | C18, C19, C44, C45 | 8pF | maru-pixracer-cache:C_Small | swi_dipol:C_0402 |  |  |  | GRM1555C1E8R0CA01D
7 | 5 | C22, C23, C24, C25, C26 | 10uF 10V | maru-pixracer-cache:C_Small | swi_dipol:C_0805 |  |  |  | C2012X5R1A106K085AB
8 | 3 | C27, C29, C47 | 1uF | maru-pixracer-cache:C_Small | swi_dipol:C_0603 |  |  |  | C1608X5R1C105K080AA
9 | 1 | C46 | 470nF | maru-pixracer-cache:C_Small | swi_dipol:C_0603 |  |  |  | GRM188R71C474KA88D
10 | 2 | C55, C56 | 47uF 16V | maru-pixracer-cache:C_Small | swi_dipol:C_0805 |  |  |  | C2012X5R1A476M125AC, LMK212BBJ476MG-T
11 | 2 | D1, D4 | RED | maru-pixracer-cache:LED | LEDs:LED_0603
12 | 1 | D2 | BAS70-02V | maru-pixracer-cache:D_Schottky | Diodes_SMD:D_SOD-523 |  |  |  | BAS70-02V-V-G-08, BAS70KFILM
13 | 1 | D3 | GREEN | maru-pixracer-cache:LED | LEDs:LED_0603
14 | 1 | D5 | BLUE | maru-pixracer-cache:LED | LEDs:LED_0603
15 | 1 | D6 | 1N4148WT | maru-pixracer-cache:D_Schottky_Small | Diodes_SMD:D_SOD-523 |  |  |  | 1N4148WT
16 | 1 | D7 | PMEG3002 | maru-pixracer-cache:D_Schottky | Diodes_SMD:D_SOD-323F |  |  |  | PMEG3002EJ,115
17 | 2 | J1, J2 | ARM Cortex JTAG 6p | maru-pixracer-cache:Conn_02x03_Odd_Even | swi_pads:Tag-Connect_TC2030-IDC-NL-NOHOLE
18 | 1 | J3 | BRICK | maru-pixracer-cache:Conn_01x04 | Pin_Headers:Pin_Header_Straight_1x04_Pitch2.54mm
19 | 1 | J4 | Micro_SD_Card | maru-pixracer-cache:Micro_SD_Card | swi_sdcard:DM3CS-SF |  |  |  | DM3CS-SF
20 | 1 | J5 | IO_CHANNELS | maru-pixracer-cache:Conn_01x08 | Pin_Headers:Pin_Header_Straight_1x08_Pitch2.54mm
21 | 1 | J6 | VDD_SERVO | maru-pixracer-cache:Conn_01x08 | Pin_Headers:Pin_Header_Straight_1x08_Pitch2.54mm
22 | 1 | J7 | SERVO_GND | maru-pixracer-cache:Conn_01x08 | Pin_Headers:Pin_Header_Straight_1x08_Pitch2.54mm
23 | 1 | J8 | SAFETY | maru-pixracer-cache:Conn_01x03 | Pin_Headers:Pin_Header_Straight_1x03_Pitch2.54mm
24 | 1 | J9 | CH1-3 | maru-pixracer-cache:Conn_01x04 | Pin_Headers:Pin_Header_Straight_1x04_Pitch2.54mm
25 | 1 | J10 | CH4-6 | maru-pixracer-cache:Conn_01x04 | Pin_Headers:Pin_Header_Straight_1x04_Pitch2.54mm
26 | 1 | J11 | BUZZ | maru-pixracer-cache:Conn_01x03 | Pin_Headers:Pin_Header_Straight_1x03_Pitch2.54mm
27 | 1 | J12 | AIR | maru-pixracer-cache:Conn_01x03 | Pin_Headers:Pin_Header_Straight_1x03_Pitch2.54mm
28 | 1 | J13 | AUX-ADC1 | maru-pixracer-cache:Conn_01x02 | Pin_Headers:Pin_Header_Straight_1x02_Pitch2.54mm
29 | 1 | J14 | AUX-ADC2 | maru-pixracer-cache:Conn_01x02 | Pin_Headers:Pin_Header_Straight_1x02_Pitch2.54mm
30 | 1 | J15 | SIPI | maru-pixracer-cache:Conn_01x03 | Pin_Headers:Pin_Header_Straight_1x03_Pitch2.54mm
31 | 1 | J16 | SPEKT | maru-pixracer-cache:Conn_01x03 | Pin_Headers:Pin_Header_Straight_1x03_Pitch2.54mm
32 | 1 | J17 | SERIAL1 | maru-pixracer-cache:Conn_01x06 | Connectors_JST:JST_GH_SM06B-GHS-TB_06x1.25mm_Angled |  |  |  | SM06B-GHS-TB(LF)(SN)
33 | 1 | J18 | TELEM2 | maru-pixracer-cache:Conn_01x06 | Pin_Headers:Pin_Header_Straight_1x06_Pitch2.54mm
34 | 1 | J19 | CAN | maru-pixracer-cache:Conn_01x04 | Connectors_JST:JST_GH_SM04B-GHS-TB_04x1.25mm_Angled |  |  |  | SM04B-GHS-TB(LF)(SN)-
35 | 1 | J20 | SERIAL4 | maru-pixracer-cache:Conn_01x04 | Pin_Headers:Pin_Header_Straight_1x04_Pitch2.54mm
36 | 1 | J21 | SERIAL5 | maru-pixracer-cache:Conn_01x04 | Pin_Headers:Pin_Header_Straight_1x04_Pitch2.54mm
37 | 1 | J22 | GPS/I2C | maru-pixracer-cache:Conn_01x06 | Connectors_JST:JST_GH_SM06B-GHS-TB_06x1.25mm_Angled |  |  |  | SM06B-GHS-TB(LF)(SN)
38 | 1 | J23 | SORI | maru-pixracer-cache:Conn_01x03 | Pin_Headers:Pin_Header_Straight_1x03_Pitch2.54mm
39 | 1 | LOGO1 | OPEN_HARDWARE_1 | maru-pixracer-cache:OPEN_HARDWARE_1 | Symbols:OSHW-Logo_5.7x6mm_SilkScreen
40 | 4 | M1, M2, M3, M4 | MOUNTING-HOLE | maru-pixracer-cache:MOUNTING-HOLE | Mounting_Holes:MountingHole_3.2mm_M3
41 | 1 | P1 | USB_OTG | maru-pixracer-cache:pkl_USB_OTG | pkl_connectors:Connector_USB_Micro_B_SMD |  |  |  | 10118192-0001LF
42 | 1 | Q1 | SI3493BDV | maru-pixracer-cache:SI3493BDV | Housings_SSOP:TSOP-6_1.65x3.05mm_Pitch0.95mm | https://www.vishay.com/docs/74478/si3493bdv.pdf |  |  | SI3493BDV-T1-E3
43 | 1 | Q2 | DMG1012UW | maru-pixracer-cache:2N7002 | TO_SOT_Packages_SMD:SOT-323_SC-70 |  | 621-DMG1012UW-7 |  | DMG1012UW-7
44 | 5 | R1, R4, R34, R35, R38 | 470 | maru-pixracer-cache:R_Small | swi_dipol:R_0402_NoSilk |  |  |  | ERJ-2GEJ471X
45 | 15 | R2, R8, R9, R12, R13, R14, R33, R45, R46, R48, R49, R50, R51, R52, R64 | 10K | maru-pixracer-cache:R_Small | swi_dipol:R_0402_NoSilk |  |  |  | RC1005J103CS
46 | 1 | R5 | 200 1% | maru-pixracer-cache:R_Small | swi_dipol:R_0402_NoSilk | https://industrial.panasonic.com/cdbs/www-data/pdf/RDA0000/AOA0000C304.pdf |  |  | ERJ-2RKF2000X
47 | 1 | R6 | 1K 1% | maru-pixracer-cache:R_Small | swi_dipol:R_0402_NoSilk |  |  |  | ERJ-2RKF1001X
48 | 6 | R7, R16, R17, R18, R19, R20 | 100K | maru-pixracer-cache:R_Small | swi_dipol:R_0402_NoSilk |  |  |  | ERJ-2GEJ104X
49 | 2 | R10, R11 | 470K | maru-pixracer-cache:R_Small | swi_dipol:R_0402_NoSilk |  |  |  | ERJ-2GEJ474X
50 | 3 | R15, R29, R30 | 1K | maru-pixracer-cache:R_Small | swi_dipol:R_0402_NoSilk |  |  |  | ERJ-2GEJ102X
51 | 1 | R21 | DNP | maru-pixracer-cache:R_Small | swi_dipol:R_0805 |  |  |  | -
52 | 2 | R22, R23 | 220 | maru-pixracer-cache:R_Small | swi_dipol:R_0805 |  |  |  | RC2012J221CS
53 | 1 | R24 | 2K7 | maru-pixracer-cache:R_Small | swi_dipol:R_0402_NoSilk |  |  |  | ERJ-2GEJ272X
54 | 2 | R25, R26 | 1M | maru-pixracer-cache:R_Small | swi_dipol:R_0402_NoSilk |  |  |  | ERJ-2GEJ105X
55 | 2 | R27, R28 | 22 | maru-pixracer-cache:R_Small | swi_dipol:R_0402_NoSilk |  |  |  | ERJ-2GEJ220X
56 | 24 | R31, R32, R39, R40, R41, R42, R43, R44, R53, R54, R55, R56, R57, R58, R59, R60, R61, R65, R68, R69, R70, R71, R72, R73 | 220 | maru-pixracer-cache:R_Small | swi_dipol:R_0402_NoSilk |  |  |  | ERJ-2GEJ221X
57 | 1 | R36 | 47 | maru-pixracer-cache:R_Small | swi_dipol:R_0402_NoSilk |  |  |  | ERJ-2GEJ470X
58 | 3 | R37, R66, R67 | 1K5 | maru-pixracer-cache:R_Small | swi_dipol:R_0402_NoSilk |  |  |  | ERJ-2GEJ152X
59 | 1 | R47 | 10 | maru-pixracer-cache:R_Small | swi_dipol:R_0402_NoSilk |  |  |  | ERJ-2GEJ100X
60 | 1 | R62 | 100 | maru-pixracer-cache:R_Small | swi_dipol:R_0402_NoSilk |  |  |  | ERJ-2GEJ101X
61 | 1 | R63 | 120 | maru-pixracer-cache:R | swi_dipol:R_0402_NoSilk |  |  |  | ERJ-2GEJ121X
62 | 1 | RN1 | 220 | maru-pixracer-cache:R_Pack08 | Resistors_SMD:R_Cat16-8 | http://www.bourns.com/docs/Product-Datasheets/CATCAY.pdf |  |  | CAT16-221J8LF
63 | 1 | U1 | LTC4415 | maru-pixracer-cache:LTC4415 | Housings_SSOP:MSOP-16-1EP_3x4mm_Pitch0.5mm | http://cds.linear.com/docs/en/datasheet/4415fa.pdf |  |  | LTC4415EMSE#PBF
64 | 1 | U2 | TPS2062 | maru-pixracer-cache:TPS2062 | Housings_SSOP:MSOP-8-1EP_3x3mm_Pitch0.65mm | http://www.ti.com/lit/ds/symlink/tps2062c.pdf |  |  | TPS2062CDGNR
65 | 1 | U3 | STM32F427VIT6 | maru-pixracer-cache:STM32F427VIT6 | swi_housings_qfp:LQFP-100-L_14x14mm_Pitch0.5mm |  |  |  | STM32F427VIT6
66 | 4 | U4, U5, U6, U7 | LP5907 | maru-pixracer-cache:LP5907 | TO_SOT_Packages_SMD:SOT-23-5 | http://www.ti.com/lit/ds/symlink/lp5907.pdf |  |  | LP5907QMFX-3.3Q1
67 | 1 | U8 | FM25V02A-G | maru-pixracer-cache:M25P16-VME | Housings_SOIC:SOIC-8_3.9x4.9mm_Pitch1.27mm |  |  |  | FM25V02A-G
68 | 1 | U9 | DORCA30 | maru-pixracer-cache:DORCA30 | swi_housings_qfp:QFN-24_4x4mm_Pitch0.5mm
69 | 1 | U10 | MS5611-01BA03 | maru-pixracer-cache:MS5611-01BA03 | swi_sensors:ms5611-01ba03 |  |  |  | MS561101BA03-50
70 | 1 | U11 | STM32F100C8T6 | maru-pixracer-cache:STM32F100C8T6 | swi_housings_qfp:LQFP-48-L_7x7mm_Pitch0.5mm |  |  |  | STM32F100C8T6B
71 | 1 | U12 | ICM-20602 | maru-pixracer-cache:ICM-20602 | swi_sensors:LGA-16_3x3mm_Pitch0.5mm | https://www.invensense.com/wp-content/uploads/2015/12/ICM-20602-Product-Brief-v1.0.pdf |  | 1428-1060-1-ND | ICM-20602
72 | 1 | U13 | TJA1051TK/3 | maru-pixracer-cache:TJA1051TK/3 | Housings_DFN_QFN:DFN-8-1EP_3x3mm_Pitch0.65mm |  |  | 568-8686-1-ND | TJA1051TK/3,118
73 | 1 | U14 | 74LVC2G240 | maru-pixracer-cache:74LVC2G240 | Housings_SSOP:TSSOP-8_3x3mm_Pitch0.65mm |  |  |  | 74LVC2G240DP,125
74 | 1 | U15 | MPU-9250 | maru-pixracer-cache:MPU-9250 | swi_sensors:QFN-24_3x3mm_Pitch0.4mm_large_pads |  |  | 1428-1019-1-ND | MPU-9250
75 | 2 | X1, X2 | 24MHz | maru-pixracer-cache:swi_XTAL_XGXG | swi_misc:ABM8 |  |  |  | NX3225SA-24.000MHZ-STD-CSR-1

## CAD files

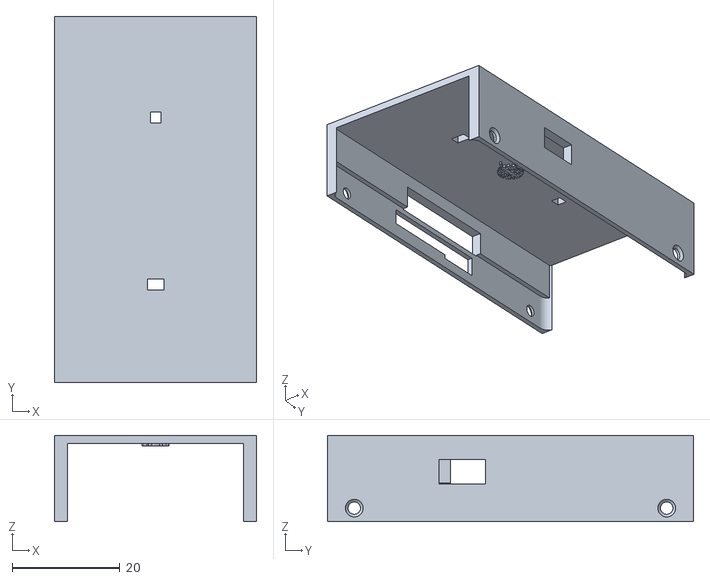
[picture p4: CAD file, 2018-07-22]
case/maru-x21-top-case.stl
37.5 x 68.0 x 16.0

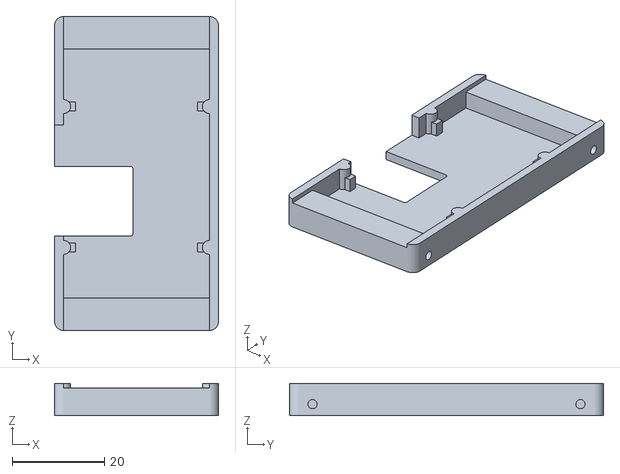
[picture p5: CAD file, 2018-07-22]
case/maru-x21-bottom-case.stl
35.5 x 68.0 x 7.00

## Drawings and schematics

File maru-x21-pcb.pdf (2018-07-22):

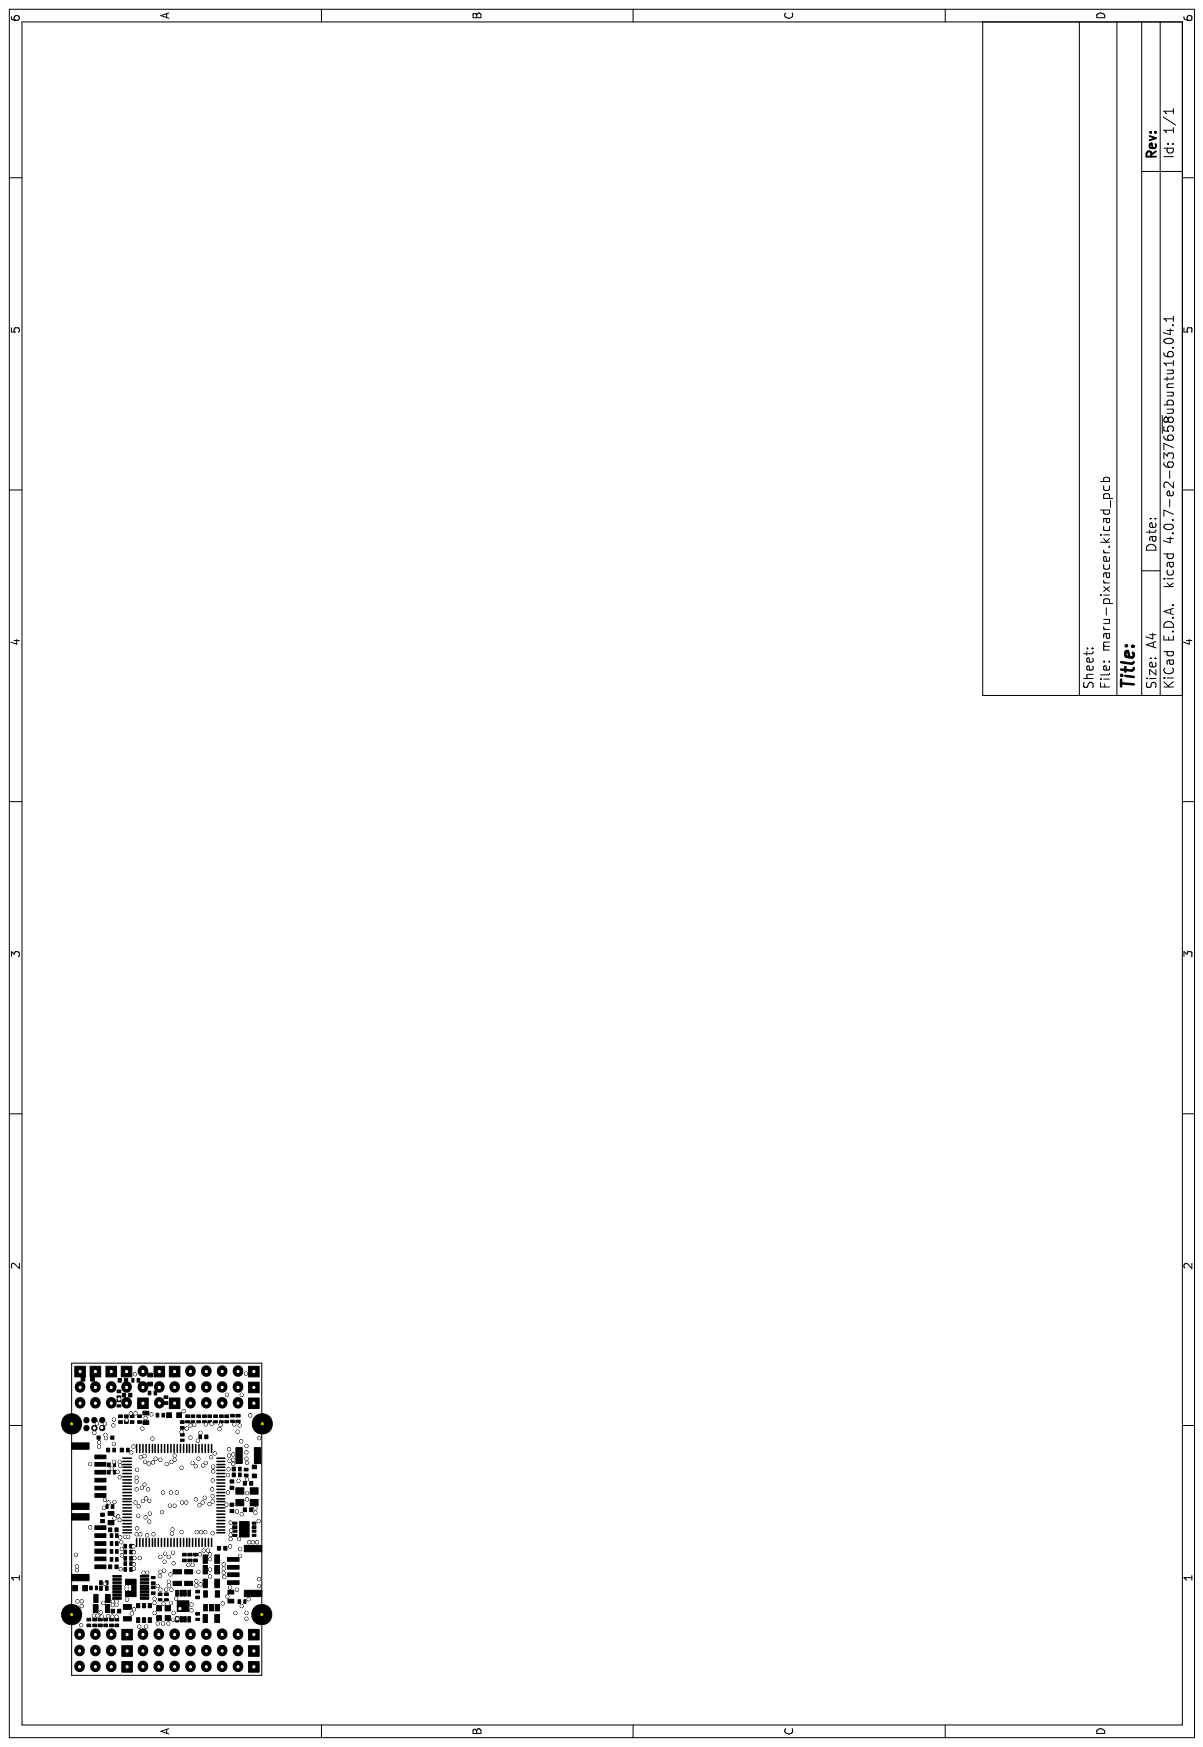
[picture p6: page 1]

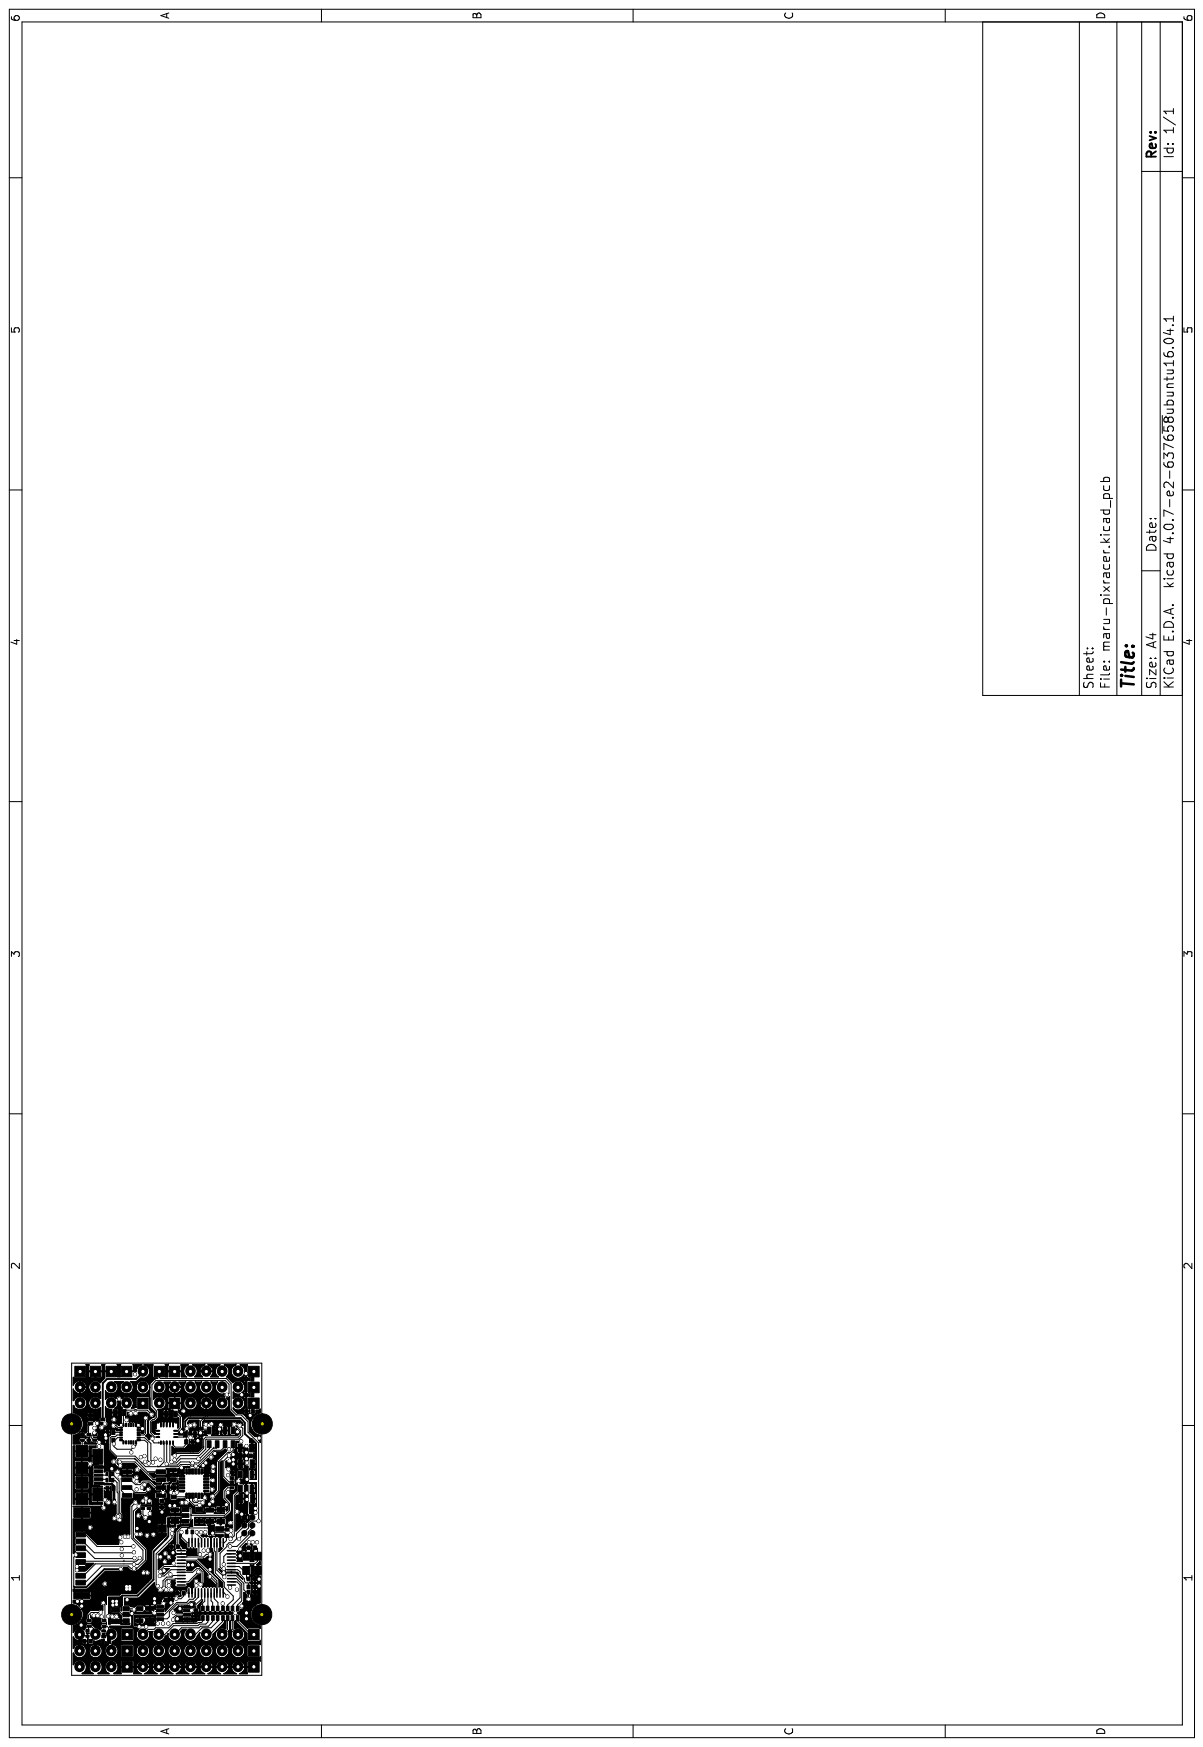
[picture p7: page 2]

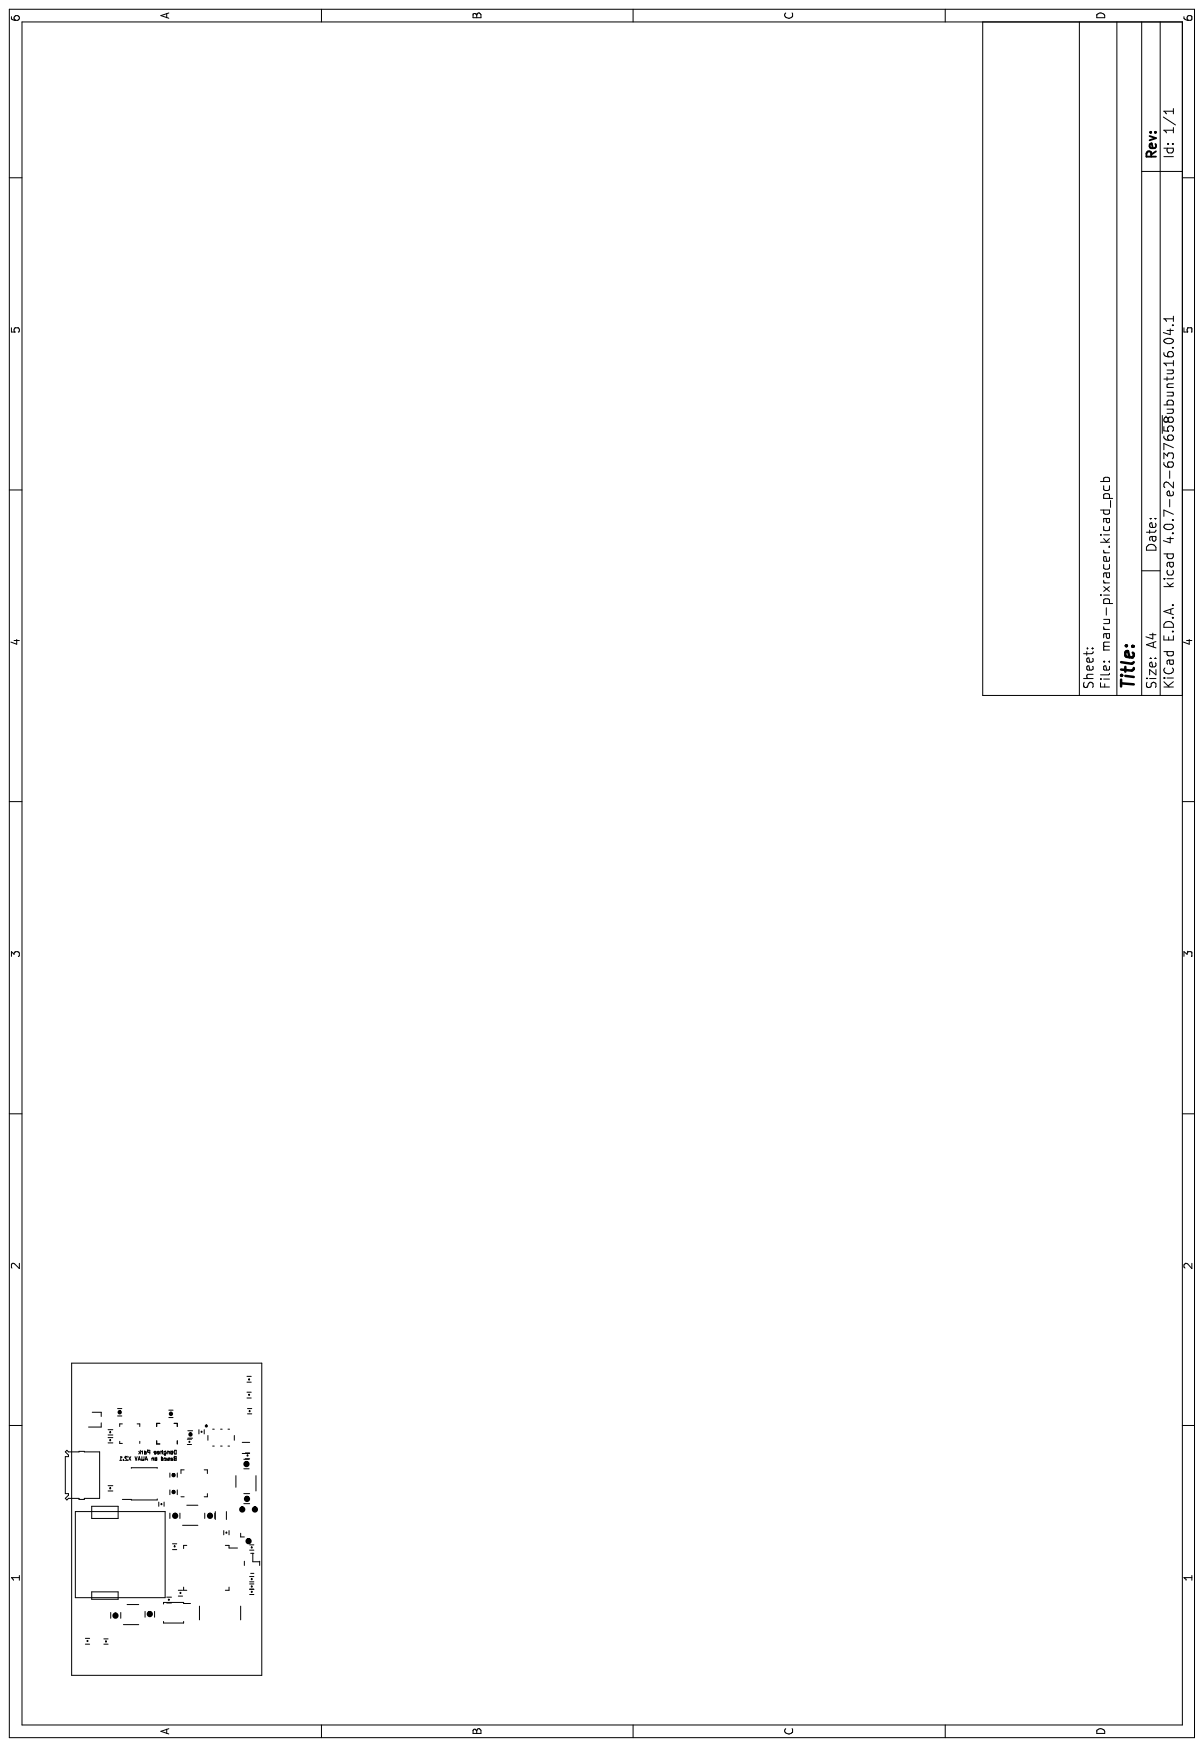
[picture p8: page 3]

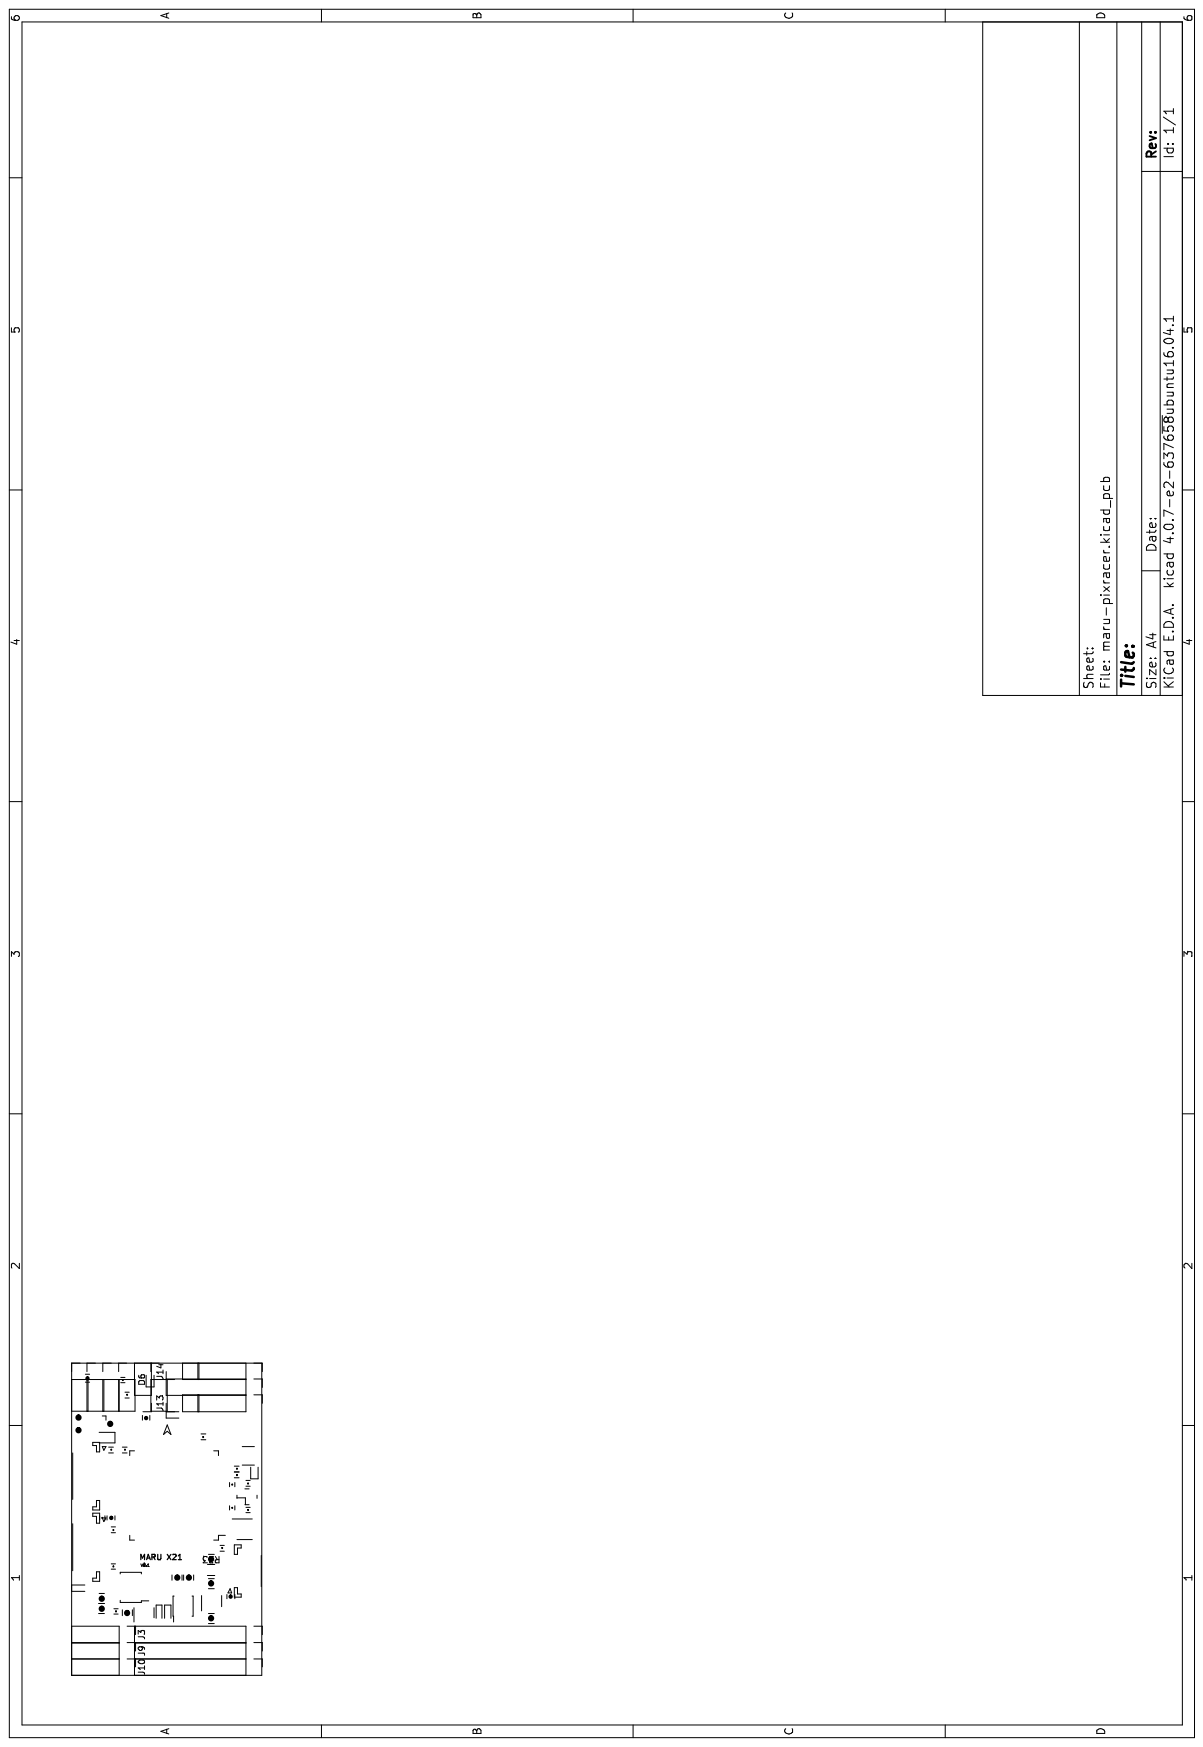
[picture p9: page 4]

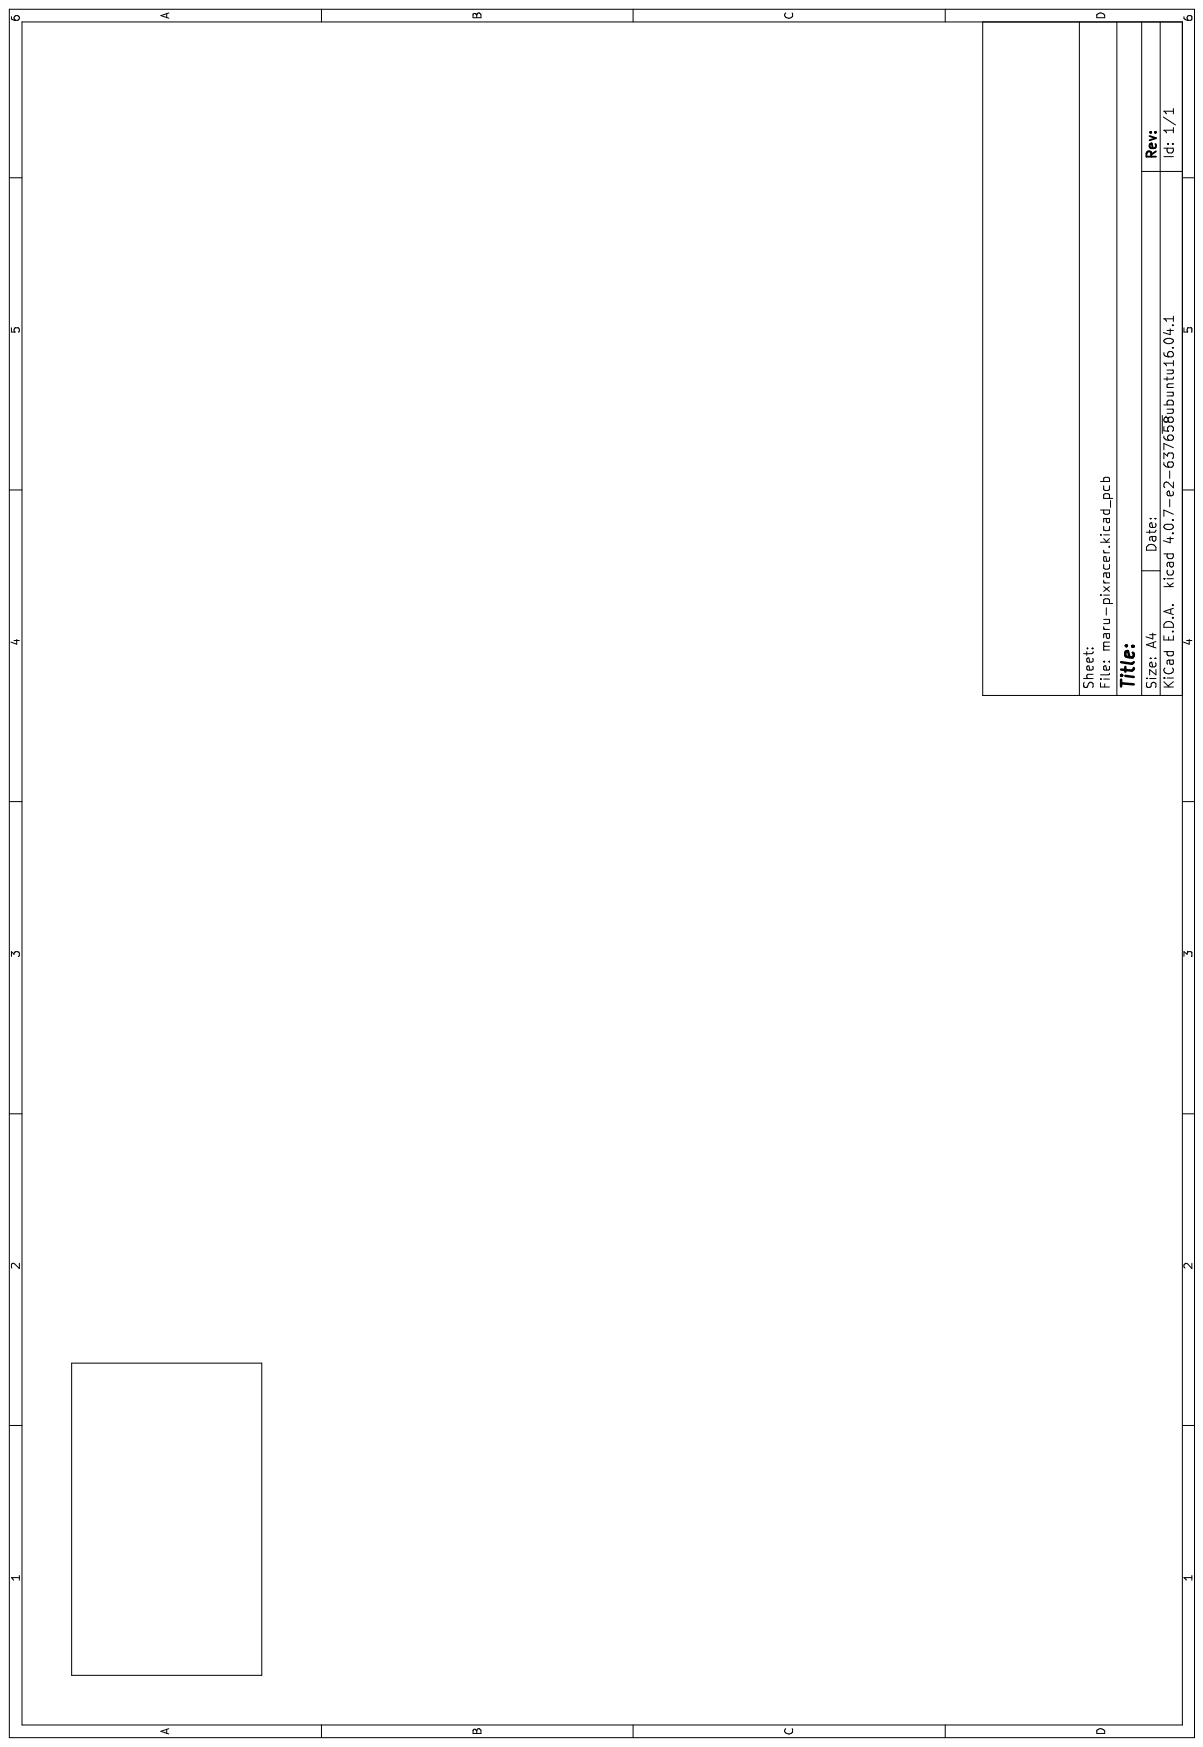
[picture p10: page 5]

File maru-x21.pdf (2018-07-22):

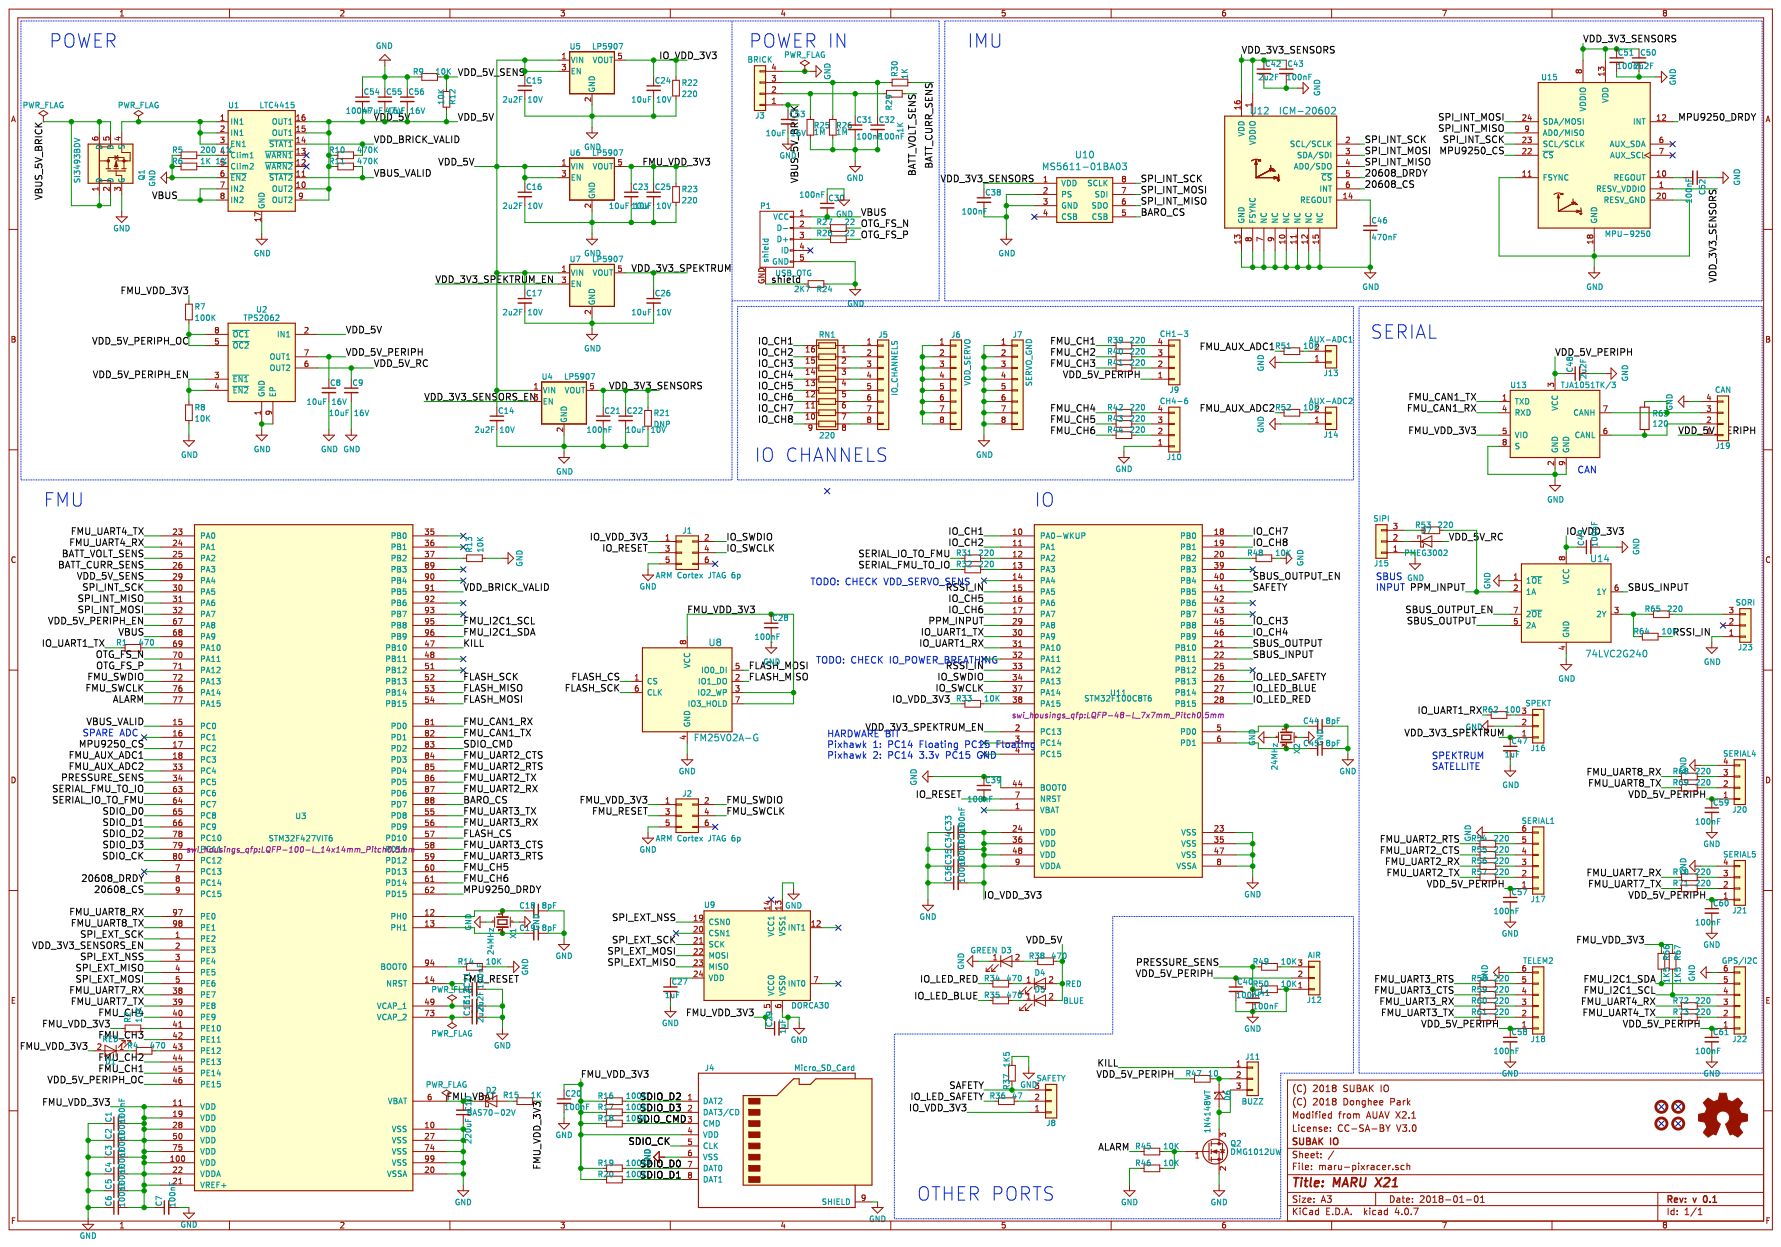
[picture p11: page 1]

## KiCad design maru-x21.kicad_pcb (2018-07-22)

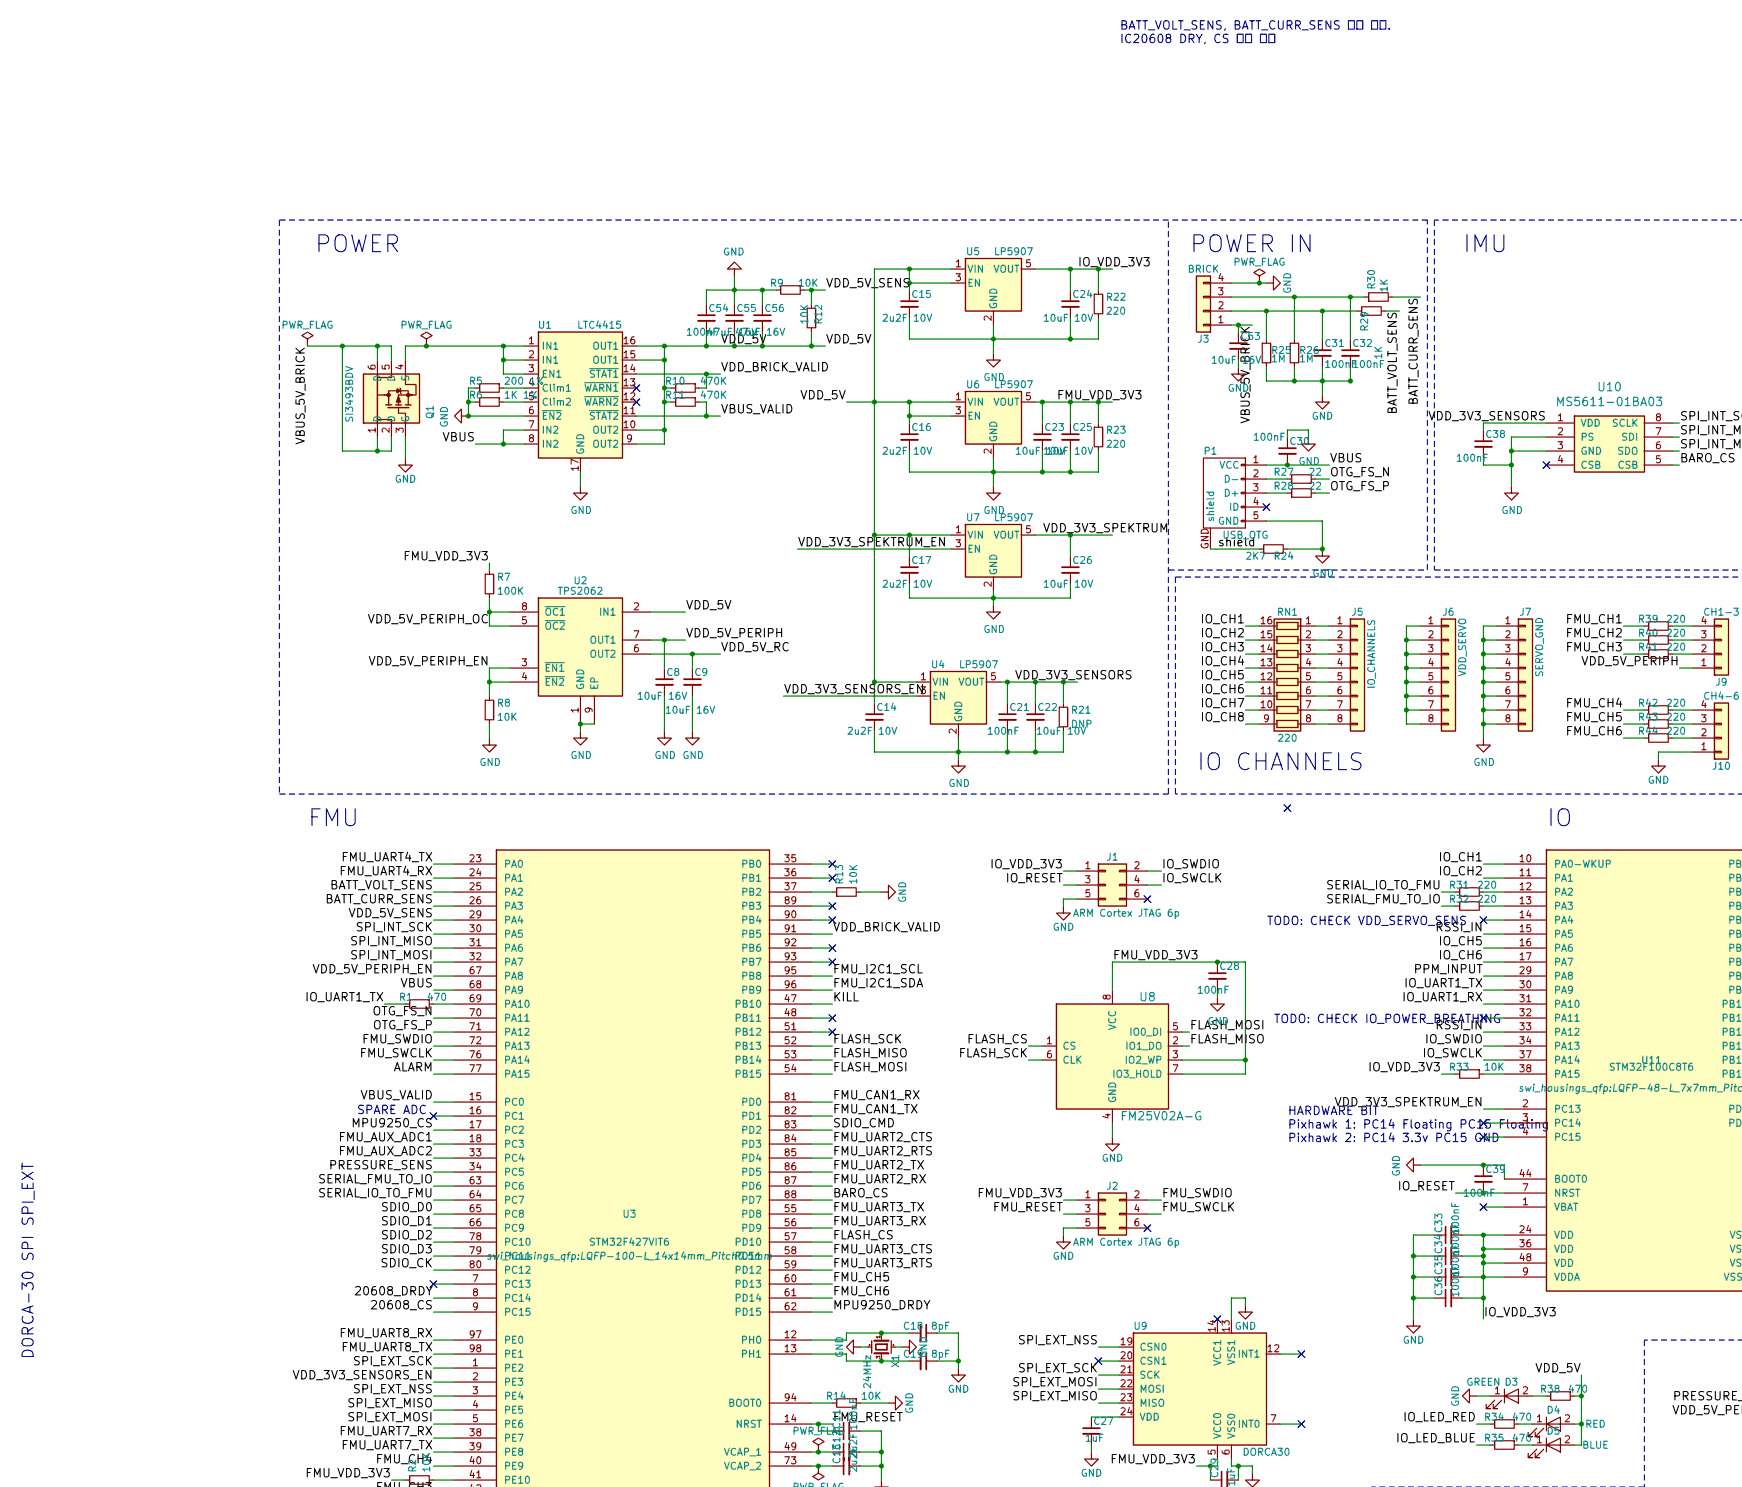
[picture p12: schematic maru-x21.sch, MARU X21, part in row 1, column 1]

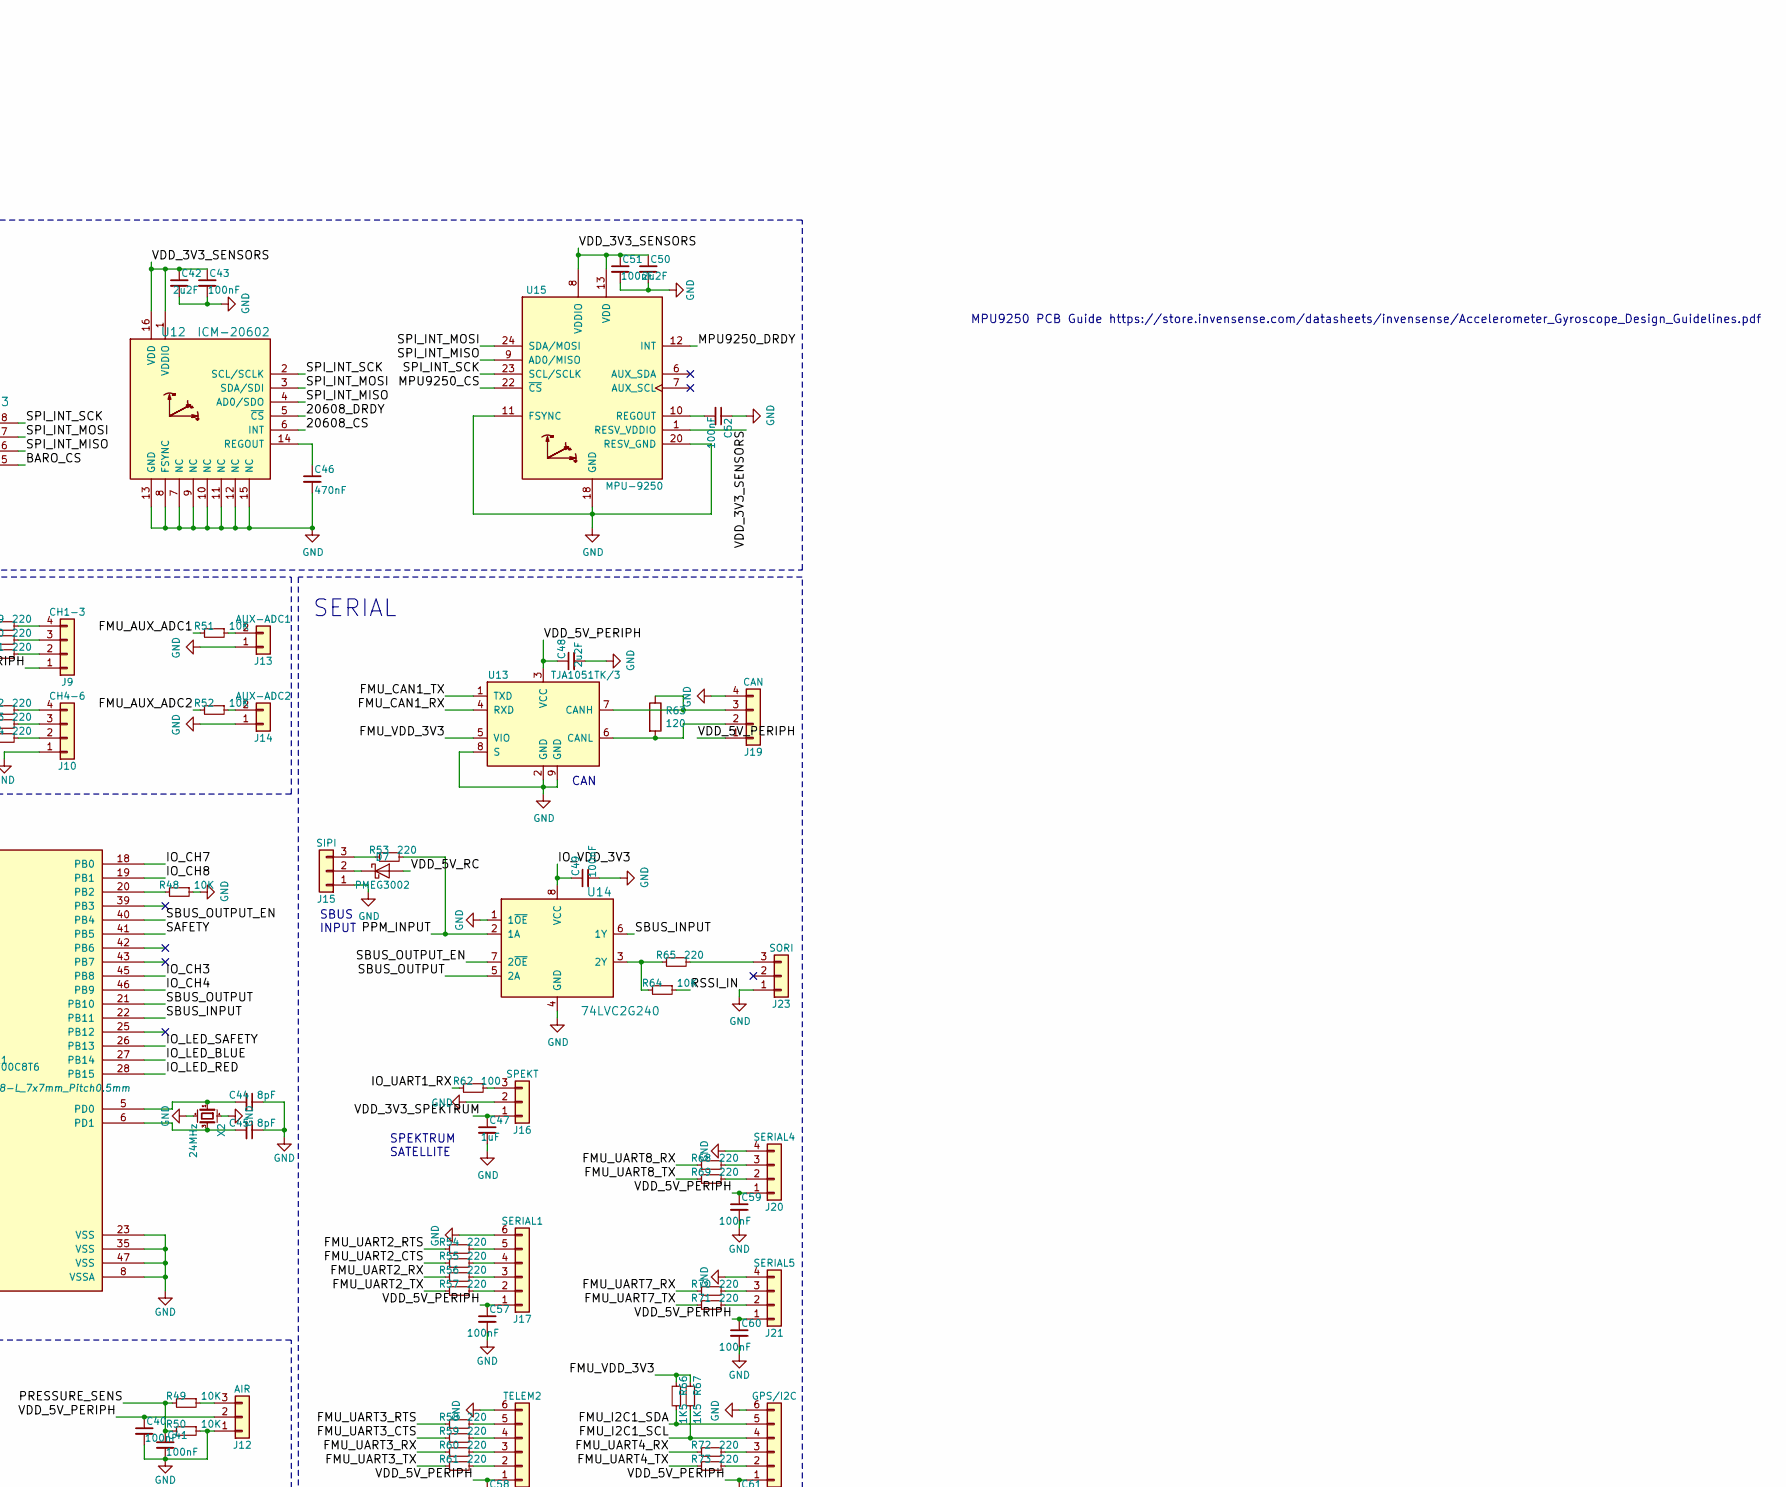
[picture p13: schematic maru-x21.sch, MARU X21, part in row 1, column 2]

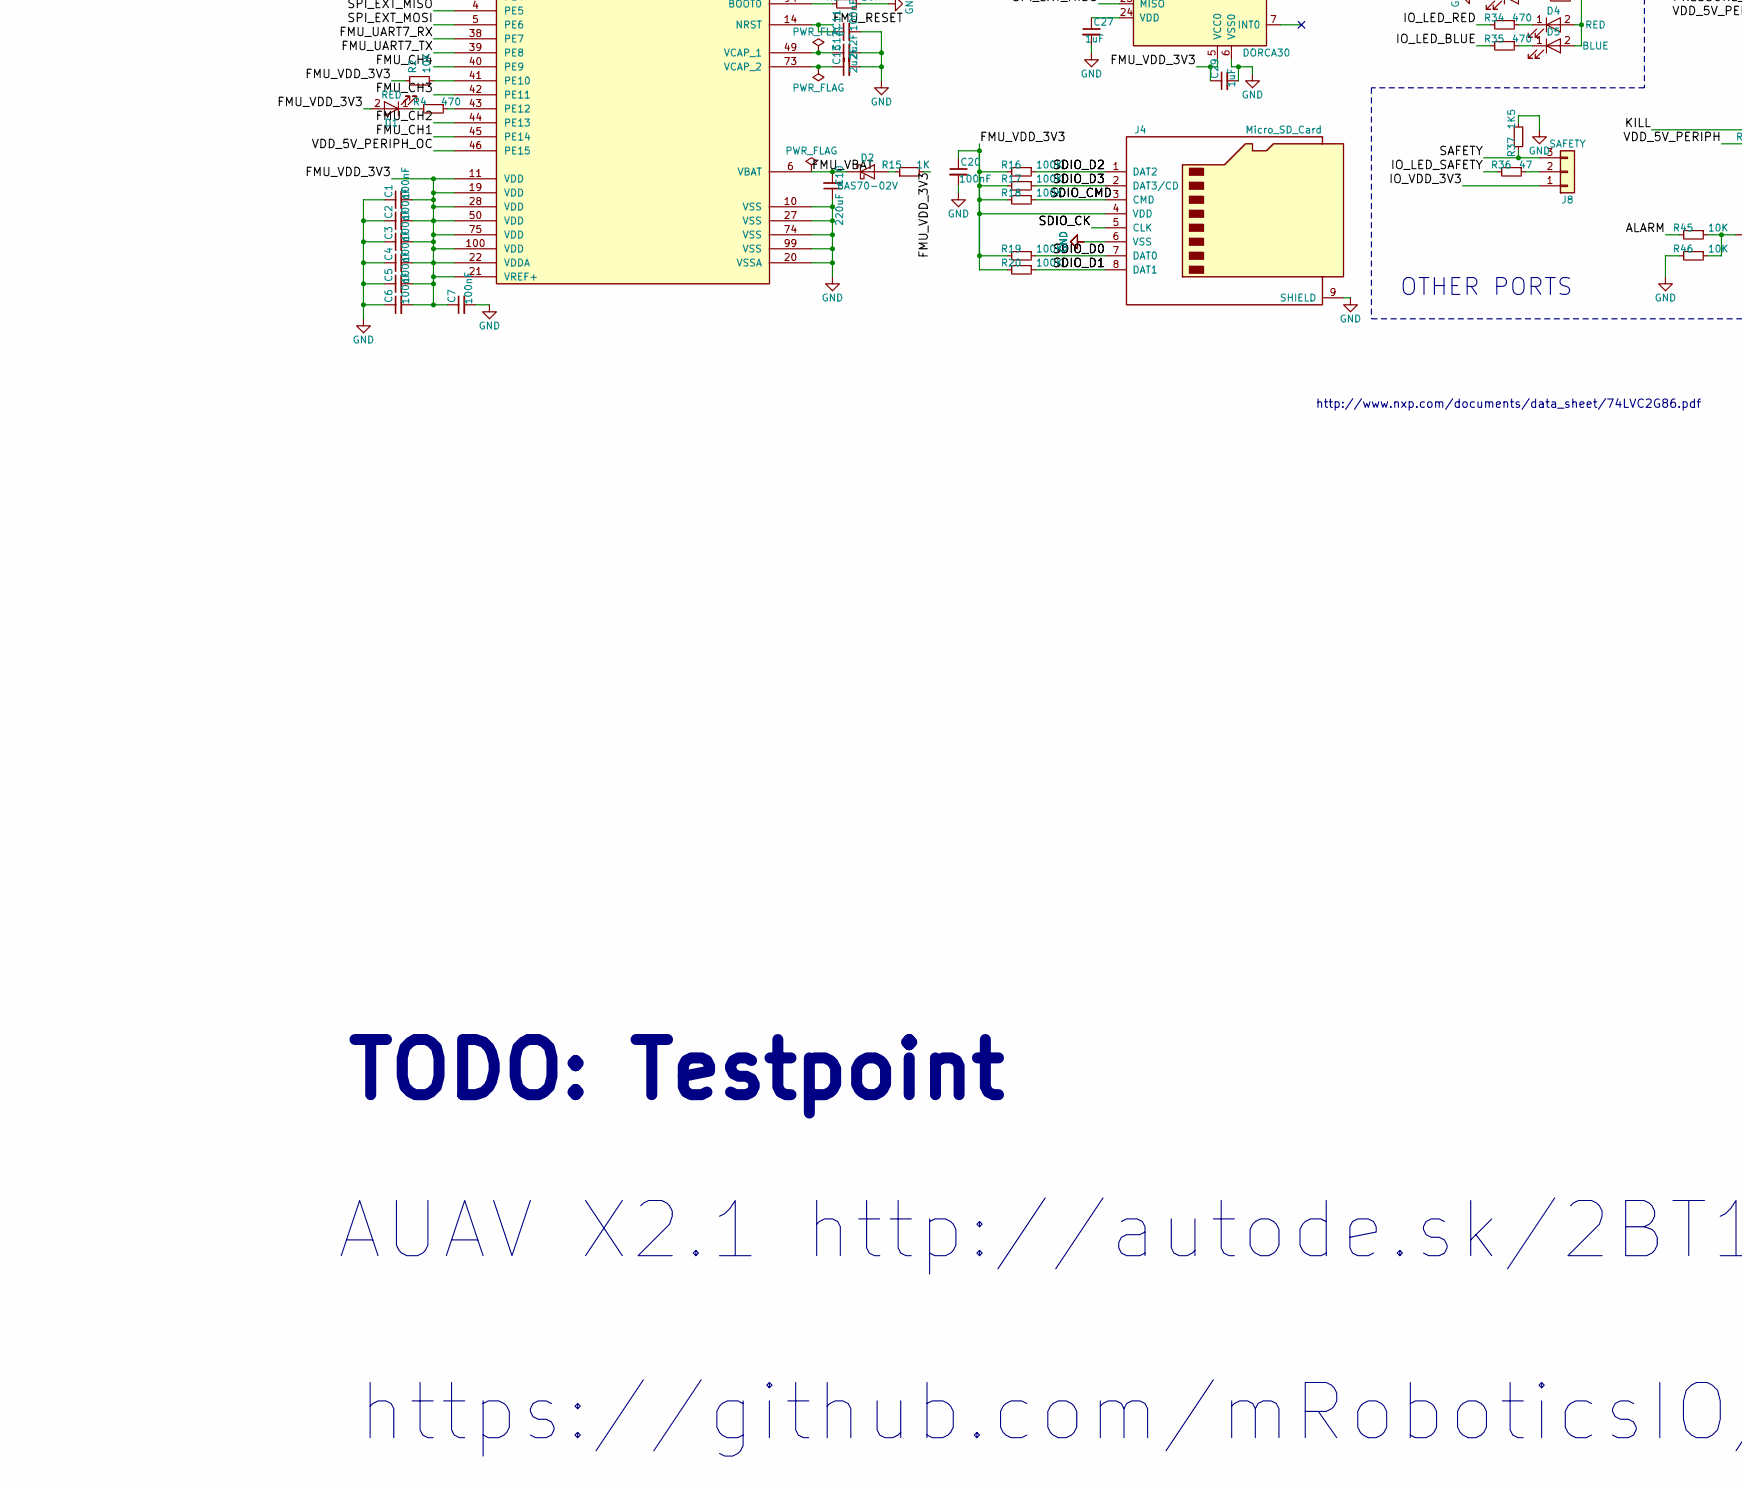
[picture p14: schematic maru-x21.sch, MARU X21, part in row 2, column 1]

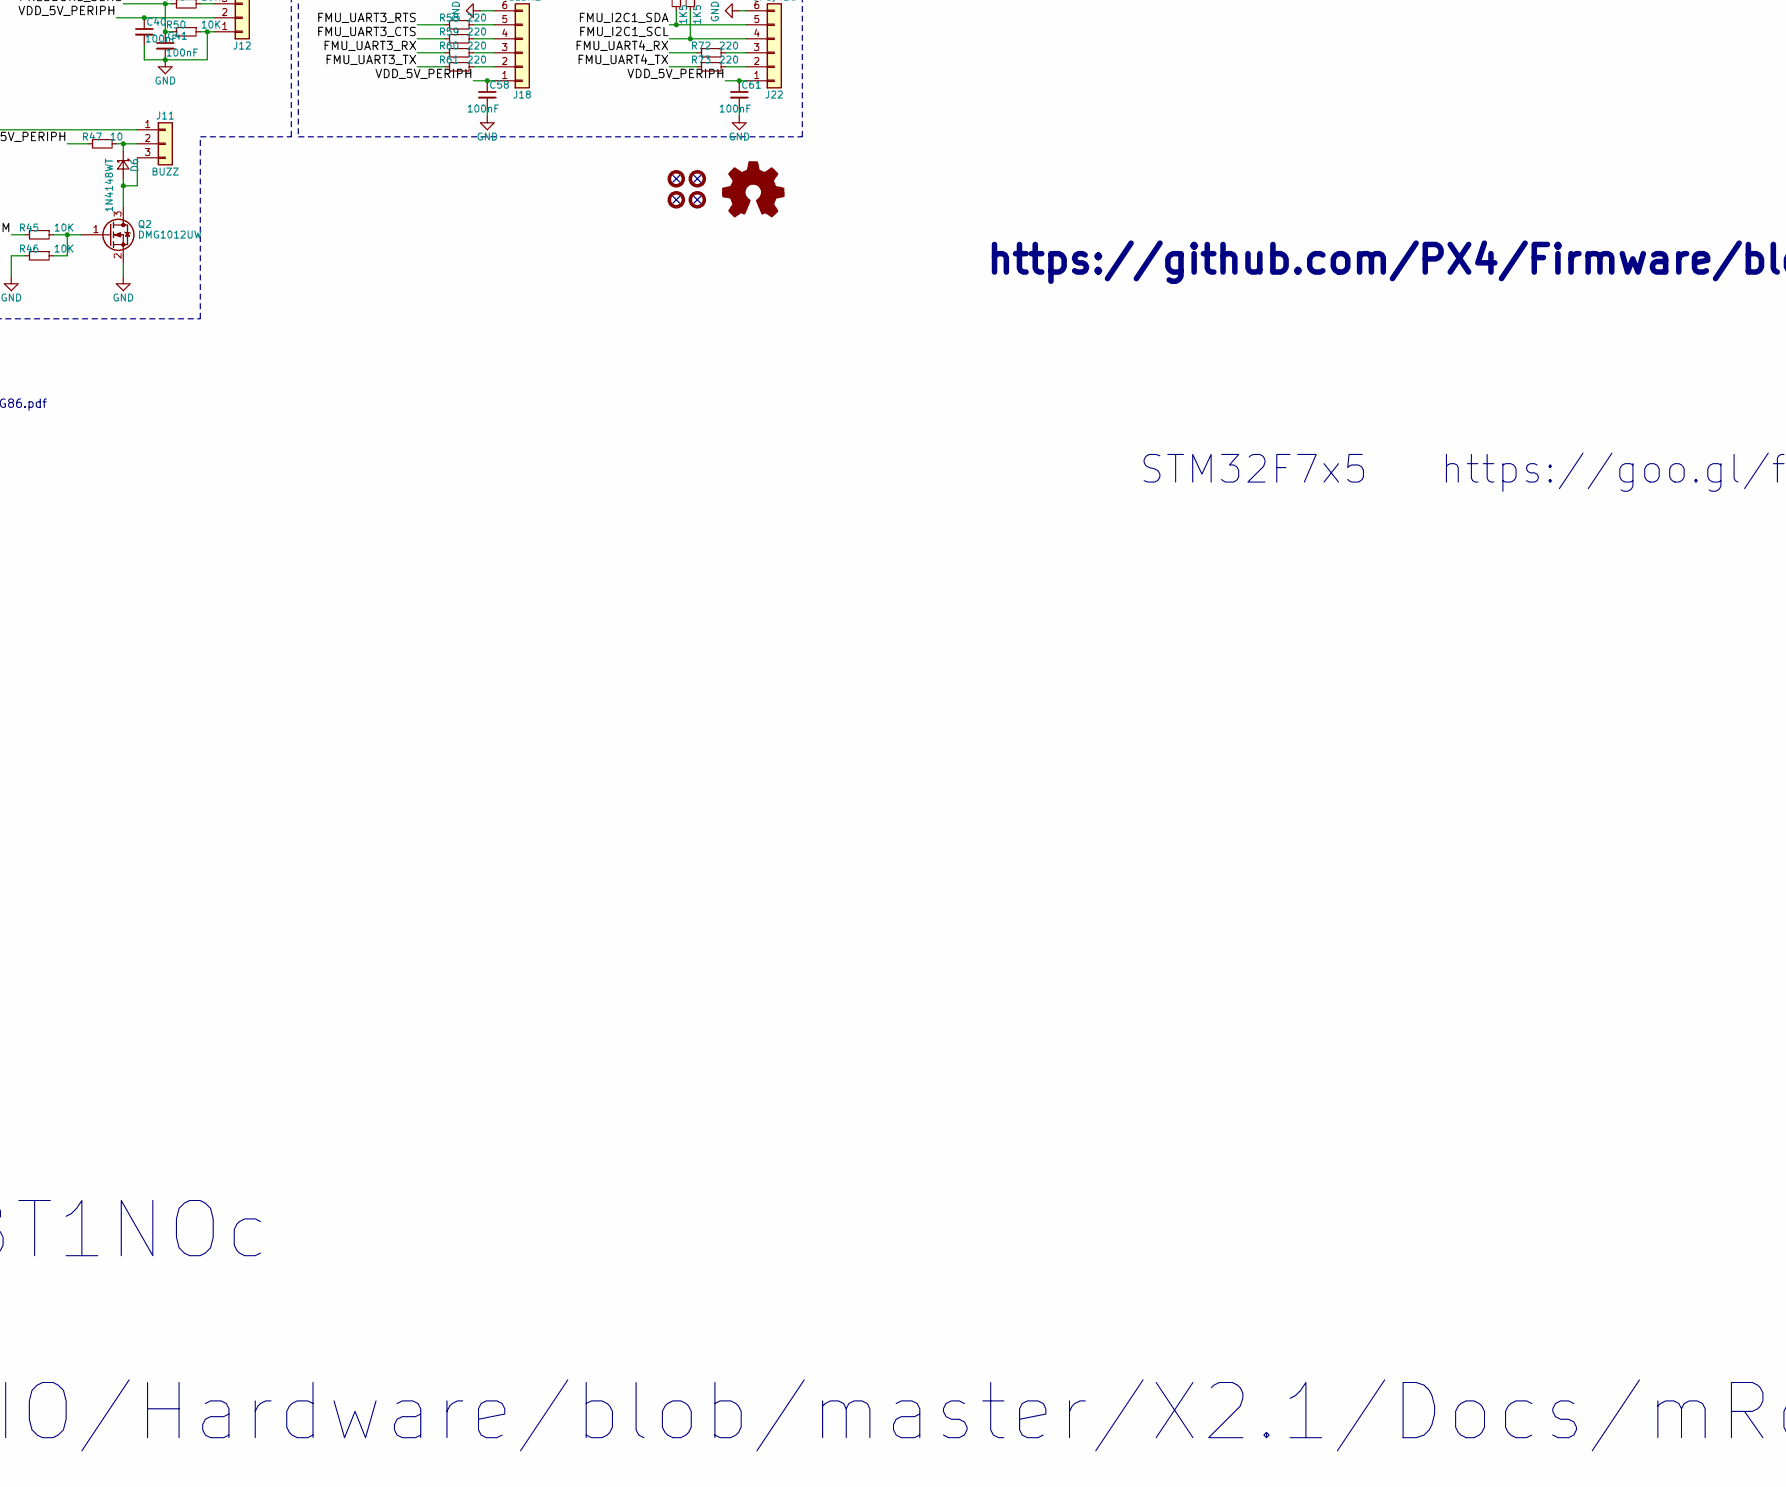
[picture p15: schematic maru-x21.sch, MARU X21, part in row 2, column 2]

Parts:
C1, C2, C3, C4, C5, C6, C7, C11, C20, C21, C28, C30, C31, C32, C33, C34, C35, C36, C38, C39, C40, C41, C43, C49, C51, C52, C54, C57, C58, C59, C60, C61: 100nF; C_0402
C8, C9, C53: 10uF 16V; C_0805
C10: 220uF; C_1210
C12, C13, C42, C48, C50: 2u2F; C_0603
C14, C15, C16, C17: 2u2F 10V; C_0805
C18, C19, C44, C45: 8pF; C_0402
C22, C23, C24, C25, C26: 10uF 10V; C_0805
C27, C29, C47: 1uF; C_0603
C46: 470nF; C_0603
C55, C56: 47uF 16V; C_0805
D1, D4: RED; LED_0603
D2: BAS70-02V; D_SOD-523
D3: GREEN; LED_0603
D5: BLUE; LED_0603
D6: 1N4148WT; D_SOD-523
D7: PMEG3002; D_SOD-323F
J1, J2: ARM Cortex JTAG 6p; Tag-Connect_TC2030-IDC-NL-NOHOLE
J3: BRICK; Pin_Header_Straight_1x04_Pitch2.54mm
J4: Micro_SD_Card; DM3CS-SF
J5: IO_CHANNELS; Pin_Header_Straight_1x08_Pitch2.54mm
J6: VDD_SERVO; Pin_Header_Straight_1x08_Pitch2.54mm
J7: SERVO_GND; Pin_Header_Straight_1x08_Pitch2.54mm
J8: SAFETY; Pin_Header_Straight_1x03_Pitch2.54mm
J9: CH1-3; Pin_Header_Straight_1x04_Pitch2.54mm
J10: CH4-6; Pin_Header_Straight_1x04_Pitch2.54mm
J11: BUZZ; Pin_Header_Straight_1x03_Pitch2.54mm
J12: AIR; Pin_Header_Straight_1x03_Pitch2.54mm
J13: AUX-ADC1; Pin_Header_Straight_1x02_Pitch2.54mm
J14: AUX-ADC2; Pin_Header_Straight_1x02_Pitch2.54mm
J15: SIPI; Pin_Header_Straight_1x03_Pitch2.54mm
J16: SPEKT; Pin_Header_Straight_1x03_Pitch2.54mm
J17: SERIAL1; JST_GH_SM06B-GHS-TB_06x1.25mm_Angled
J18: TELEM2; Pin_Header_Straight_1x06_Pitch2.54mm
J19: CAN; JST_GH_SM04B-GHS-TB_04x1.25mm_Angled
J20: SERIAL4; Pin_Header_Straight_1x04_Pitch2.54mm
J21: SERIAL5; Pin_Header_Straight_1x04_Pitch2.54mm
J22: GPS/I2C; JST_GH_SM06B-GHS-TB_06x1.25mm_Angled
J23: SORI; Pin_Header_Straight_1x03_Pitch2.54mm
LOGO1: OPEN_HARDWARE_1; OSHW-Logo_5.7x6mm_SilkScreen
M1, M2, M3, M4: MOUNTING-HOLE; MountingHole_3.2mm_M3
P1: USB_OTG; Connector_USB_Micro_B_SMD
Q1: SI3493BDV; TSOP-6_1.65x3.05mm_Pitch0.95mm
Q2: DMG1012UW; SOT-323_SC-70
R1, R4, R34, R35, R38: 470; R_0402_NoSilk
R2, R8, R9, R12, R13, R14, R33, R45, R46, R48, R49, R50, R51, R52, R64: 10K; R_0402_NoSilk
R5: 200 1%; R_0402_NoSilk
R6: 1K 1%; R_0402_NoSilk
R7, R16, R17, R18, R19, R20: 100K; R_0402_NoSilk
R10, R11: 470K; R_0402_NoSilk
R15, R29, R30: 1K; R_0402_NoSilk
R21: DNP; R_0805
R22, R23: 220; R_0805
R24: 2K7; R_0402_NoSilk
R25, R26: 1M; R_0402_NoSilk
R27, R28: 22; R_0402_NoSilk
R31, R32, R39, R40, R41, R42, R43, R44, R53, R54, R55, R56, R57, R58, R59, R60, R61, R65, R68, R69, R70, R71, R72, R73: 220; R_0402_NoSilk
R36: 47; R_0402_NoSilk
R37, R66, R67: 1K5; R_0402_NoSilk
R47: 10; R_0402_NoSilk
R62: 100; R_0402_NoSilk
R63: 120; R_0402_NoSilk
RN1: 220; R_Cat16-8
U1: LTC4415; MSOP-16-1EP_3x4mm_Pitch0.5mm
U2: TPS2062; MSOP-8-1EP_3x3mm_Pitch0.65mm
U3: STM32F427VIT6; LQFP-100-L_14x14mm_Pitch0.5mm
U4, U5, U6, U7: LP5907; SOT-23-5
U8: FM25V02A-G; SOIC-8_3.9x4.9mm_Pitch1.27mm
U9: DORCA30; QFN-24_4x4mm_Pitch0.5mm
U10: MS5611-01BA03; ms5611-01ba03
U11: STM32F100C8T6; LQFP-48-L_7x7mm_Pitch0.5mm
U12: ICM-20602; LGA-16_3x3mm_Pitch0.5mm; digikey# 1428-1060-1-ND
U13: TJA1051TK/3; DFN-8-1EP_3x3mm_Pitch0.65mm; digikey# 568-8686-1-ND
U14: 74LVC2G240; TSSOP-8_3x3mm_Pitch0.65mm
U15: MPU-9250; QFN-24_3x3mm_Pitch0.4mm_large_pads; digikey# 1428-1019-1-ND
X1, X2: 24MHz; ABM8

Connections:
/20608_CS: U3.9 (PC15), U12.6 (INT); also elsewhere on the board
/20608_DRDY: U3.8 (PC14), U12.5 (~CS); also elsewhere on the board
/ALARM: R45.2, U3.77 (PA15)
/BARO_CS: U3.88 (PD7), U10.5 (CSB)
/BATT_CURR_SENS: R30.2, U3.26 (PA3)
/BATT_VOLT_SENS: R29.2, U3.25 (PA2)
/FLASH_CS: U3.57 (PD10), U8.1 (CS)
/FLASH_MISO: U3.53 (PB14), U8.2 (IO1_DO)
/FLASH_MOSI: U3.54 (PB15), U8.5 (IO0_DI)
/FLASH_SCK: U3.52 (PB13), U8.6 (CLK)
/FMU_AUX_ADC1: R51.2, U3.18 (PC3)
/FMU_AUX_ADC2: R52.2, U3.33 (PC4)
/FMU_CAN1_RX: U3.81 (PD0), U13.4 (RXD)
/FMU_CAN1_TX: U3.82 (PD1), U13.1 (TXD)
/FMU_CH1: R39.2, U3.45 (PE14)
/FMU_CH2: R40.2, U3.44 (PE13)
/FMU_CH3: R41.2, U3.42 (PE11)
/FMU_CH4: R42.2, U3.40 (PE9)
/FMU_CH5: R43.2, U3.60 (PD13)
/FMU_CH6: R44.2, U3.61 (PD14)
/FMU_I2C1_SCL: J22.4, R67.1, U3.95 (PB8)
/FMU_I2C1_SDA: J22.5, R66.1, U3.96 (PB9)
/FMU_RESET: C11.1, J2.3, U3.14 (NRST)
/FMU_SWCLK: J2.4, U3.76 (PA14)
/FMU_SWDIO: J2.2, U3.72 (PA13)
/FMU_UART2_CTS: R55.2, U3.84 (PD3)
/FMU_UART2_RTS: R54.2, U3.85 (PD4)
/FMU_UART2_RX: R56.2, U3.87 (PD6)
/FMU_UART2_TX: R57.2, U3.86 (PD5)
/FMU_UART3_CTS: R59.2, U3.58 (PD11)
/FMU_UART3_RTS: R58.2, U3.59 (PD12)
/FMU_UART3_RX: R60.2, U3.56 (PD9)
/FMU_UART3_TX: R61.2, U3.55 (PD8)
/FMU_UART4_RX: R72.2, U3.24 (PA1)
/FMU_UART4_TX: R73.2, U3.23 (PA0)
/FMU_UART7_RX: R70.2, U3.38 (PE7)
/FMU_UART7_TX: R71.2, U3.39 (PE8)
/FMU_UART8_RX: R68.2, U3.97 (PE0)
/FMU_UART8_TX: R69.2, U3.98 (PE1)
/FMU_VBAT: C10.2, D2.1 (K), U3.6 (VBAT)
/FMU_VDD_3V3: C1.2, C2.2, C3.2, C4.2, C5.2, C6.2, C7.1, C20.1, C23.1, C25.1, C28.1, C29.1, D1.2 (A), J2.1, J4.4 (VDD), R2.1, R7.1, R15.2, R16.2, R17.2, R18.2, R19.2, R20.2, R23.1, R66.2, R67.2, U3.11 (VDD), U3.19 (VDD), U3.21 (VREF+), U3.22 (VDDA), U3.28 (VDD), U3.50 (VDD), U3.75 (VDD), U3.100 (VDD), U6.5 (VOUT), U8.3 (IO2_WP), U8.7 (IO3_HOLD), U8.8 (VCC), U9.5 (VCC0), U13.5 (VIO)
/IO_CH1: RN1.16 (R1.2), U11.10 (PA0-WKUP)
/IO_CH2: RN1.15 (R2.2), U11.11 (PA1)
/IO_CH3: RN1.14 (R3.2), U11.45 (PB8)
/IO_CH4: RN1.13 (R4.2), U11.46 (PB9)
/IO_CH5: RN1.12 (R5.2), U11.16 (PA6)
/IO_CH6: RN1.11 (R6.2), U11.17 (PA7)
/IO_CH7: RN1.10 (R7.2), U11.18 (PB0)
/IO_CH8: RN1.9 (R8.2), U11.19 (PB1)
/IO_LED_BLUE: R35.2, U11.27 (PB14)
/IO_LED_RED: R34.2, U11.28 (PB15)
/IO_LED_SAFETY: R36.2, U11.26 (PB13)
/IO_RESET: C39.2, J1.3, U11.7 (NRST)
/IO_SWCLK: J1.4, U11.37 (PA14)
/IO_SWDIO: J1.2, U11.34 (PA13)
/IO_UART1_RX: R62.2, U11.31 (PA10)
/IO_UART1_TX: R1.2, U11.30 (PA9)
/IO_VDD_3V3: C24.1, C33.2, C34.2, C35.2, C36.2, C49.1, J1.1, J8.1, R22.1, R33.2, U5.5 (VOUT), U11.9 (VDDA), U11.24 (VDD), U11.36 (VDD), U11.48 (VDD), U14.8 (VCC)
/KILL: J11.1, U3.47 (PB10)
/MPU9250_CS: U3.17 (PC2), U15.22 (~CS)
/MPU9250_DRDY: U3.62 (PD15), U15.12 (INT)
/OTG_FS_N: R27.2, U3.70 (PA11)
/OTG_FS_P: R28.2, U3.71 (PA12)
/PPM_INPUT: R53.1, U11.29 (PA8), U14.2 (1A)
/PRESSURE_SENS: C41.1, R49.2, R50.2, U3.34 (PC5)
/RSSI_IN: R64.1, U11.15 (PA5), U11.33 (PA12)
/SAFETY: J8.3, R37.2, U11.41 (PB5)
/SBUS_INPUT: U11.22 (PB11), U14.6 (1Y)
/SBUS_OUTPUT: U11.21 (PB10), U14.5 (2A)
/SBUS_OUTPUT_EN: U11.40 (PB4), U14.7 (2~OE)
/SDIO_CK: J4.5 (CLK), U3.80 (PC12)
/SDIO_CMD: J4.3 (CMD), R18.1, U3.83 (PD2)
/SDIO_D0: J4.7 (DAT0), R19.1, U3.65 (PC8)
/SDIO_D1: J4.8 (DAT1), R20.1, U3.66 (PC9)
/SDIO_D2: J4.1 (DAT2), R16.1, U3.78 (PC10)
/SDIO_D3: J4.2 (DAT3/CD), R17.1, U3.79 (PC11)
/SERIAL_FMU_TO_IO: R32.2, U3.63 (PC6)
/SERIAL_IO_TO_FMU: R31.2, U3.64 (PC7)
/SPI_EXT_MISO: U3.4 (PE5), U9.23 (MISO)
/SPI_EXT_MOSI: U3.5 (PE6), U9.22 (MOSI)
/SPI_EXT_NSS: U3.3 (PE4), U9.19 (CSN0)
/SPI_EXT_SCK: U3.1 (PE2), U9.21 (SCK)
/SPI_INT_MISO: U3.31 (PA6), U10.6 (SDO), U12.4 (AD0/SDO), U15.9 (AD0/MISO); also elsewhere on the board
/SPI_INT_MOSI: U3.32 (PA7), U10.7 (SDI), U12.3 (SDA/SDI), U15.24 (SDA/MOSI); also elsewhere on the board
/SPI_INT_SCK: U3.30 (PA5), U10.8 (SCLK), U12.2 (SCL/SCLK), U15.23 (SCL/SCLK); also elsewhere on the board
/VBUS: C30.2, P1.1 (VCC), U1.7 (IN2), U1.8 (IN2), U3.68 (PA9)
/VBUS_5V_BRICK: C53.1, J3.1, Q1.1 (D), Q1.2 (D), Q1.5 (D), Q1.6 (D)
/VBUS_VALID: R11.1, U1.11 (~STAT2), U3.15 (PC0)
/VDD_3V3_SENSORS: C21.1, C22.1, C38.1, C42.1, C43.1, C50.1, C51.1, R21.1, U4.5 (VOUT), U10.1 (VDD), U12.1 (VDDIO), U12.16 (VDD), U15.1 (RESV_VDDIO), U15.8 (VDDIO), U15.13 (VDD); also elsewhere on the board
/VDD_3V3_SENSORS_EN: U3.2 (PE3), U4.3 (EN)
/VDD_3V3_SPEKTRUM: C26.1, C47.1, J16.1, U7.5 (VOUT)
/VDD_3V3_SPEKTRUM_EN: U7.3 (EN), U11.2 (PC13)
/VDD_5V: C14.1, C15.1, C16.1, C17.1, C54.2, C55.2, C56.2, D4.2 (A), D5.2 (A), R10.2, R11.2, R12.2, R38.1, U1.9 (OUT2), U1.10 (OUT2), U1.15 (OUT1), U1.16 (OUT1), U2.2 (IN1), U4.1 (VIN), U5.1 (VIN), U5.3 (EN), U6.1 (VIN), U6.3 (EN), U7.1 (VIN)
/VDD_5V_PERIPH: C8.1, C40.1, C48.1, C57.1, C58.1, C59.1, C60.1, C61.1, J9.1, J12.2, J17.1, J18.1, J19.1, J20.1, J21.1, J22.1, R47.2, U2.7 (OUT1), U13.3 (VCC)
/VDD_5V_PERIPH_EN: R8.1, U2.3 (~EN1), U2.4 (~EN2), U3.67 (PA8)
/VDD_5V_PERIPH_OC: R7.2, U2.5 (~OC2), U2.8 (~OC1), U3.46 (PE15)
/VDD_5V_RC: C9.1, D7.2 (A), U2.6 (OUT2)
/VDD_5V_SENS: R9.1, R12.1, U3.29 (PA4)
/VDD_BRICK_VALID: R10.1, U1.14 (~STAT1), U3.91 (PB5)
/shield: P1.GND (shield), R24.1
GND: C1.1, C2.1, C3.1, C4.1, C5.1, C6.1, C7.2, C8.2, C9.2, C10.1, C11.2, C12.2, C13.2, C14.2, C15.2, C16.2, C17.2, C18.1, C19.1, C20.2, C21.2, C22.2, C23.2, C24.2, C25.2, C26.2, C27.2, C28.2, C29.2, C30.1, C31.2, C32.2, C33.1, C34.1, C35.1, C36.1, C38.2, C39.1, C40.2, C41.2, C42.2, C43.2, C44.1, C45.1, C46.2, C47.2, C48.2, C49.2, C50.2, C51.2, C52.1, C53.2, C54.1, C55.1, C56.1, C57.2, C58.2, C59.2, C60.2, C61.2, D3.1 (K), J1.5, J2.5, J3.4, J4.6 (VSS), J4.9 (SHIELD), J7.1, J7.2, J7.3, J7.4, J7.5, J7.6, J7.7, J7.8, J10.1, J12.1, J13.1, J14.1, J15.1, J16.2, J17.6, J18.6, J19.4, J20.4, J21.4, J22.6, J23.1, P1.5 (GND), Q1.3 (G), Q2.2 (S), R5.2, R6.2, R8.2, R9.2, R13.2, R14.1, R21.2, R22.2, R23.2, R24.2, R25.2, R26.2, R37.1, R46.2, R48.1, R50.1, U1.6 (~EN2), U1.17 (GND), U2.1 (GND), U2.9 (EP), U3.10 (VSS), U3.20 (VSSA), U3.27 (VSS), U3.74 (VSS), U3.99 (VSS), U4.2 (GND), U5.2 (GND), U6.2 (GND), U7.2 (GND), U8.4 (GND), U9.6 (VSS0), U9.13 (VSS1), U10.2 (PS), U10.3 (GND), U11.8 (VSSA), U11.23 (VSS), U11.35 (VSS), U11.44 (BOOT0), U11.47 (VSS), U12.7 (NC), U12.8 (FSYNC), U12.9 (NC), U12.10 (NC), U12.11 (NC), U12.12 (NC), U12.13 (GND), U12.15 (NC), U13.2 (GND), U13.8 (S), U13.9 (GND), U14.1 (1~OE), U14.4 (GND), U15.11 (FSYNC), U15.18 (GND), U15.20 (RESV_GND), X1.2, X1.4, X2.2, X2.4; also elsewhere on the board
unnamed: C12.1, U3.49 (VCAP_1)
unnamed: C13.1, U3.73 (VCAP_2)
unnamed: C18.2, U3.12 (PH0), X1.1
unnamed: C19.2, U3.13 (PH1), X1.3
unnamed: C27.1, U9.24 (VDD)
unnamed: C31.1, J3.2, R25.1, R29.1
unnamed: C32.1, J3.3, R26.1, R30.1
unnamed: C44.2, U11.5 (PD0), X2.1
unnamed: C45.2, U11.6 (PD1), X2.3
unnamed 110: C46.1, U12.14 (REGOUT); also elsewhere on the board
unnamed: C52.2, U15.10 (REGOUT)
unnamed: D1.1 (K), R4.2
unnamed: D2.2 (A), R15.1
unnamed: D3.2 (A), R38.2
unnamed: D4.1 (K), R34.1
unnamed: D5.1 (K), R35.1
unnamed: D6.1 (K), J11.2, R47.1
unnamed: D6.2 (A), J11.3, Q2.3 (D)
unnamed: D7.1 (K), J15.2
unnamed: J5.1, RN1.1 (R1.1)
unnamed: J5.2, RN1.2 (R2.1)
unnamed: J5.3, RN1.3 (R3.1)
unnamed: J5.4, RN1.4 (R4.1)
unnamed: J5.5, RN1.5 (R5.1)
unnamed: J5.6, RN1.6 (R6.1)
unnamed: J5.7, RN1.7 (R7.1)
unnamed: J5.8, RN1.8 (R8.1)
unnamed: J6.1, J6.2, J6.3, J6.4, J6.5, J6.6, J6.7, J6.8
unnamed: J8.2, R36.1
unnamed: J9.2, R41.1
unnamed: J9.3, R40.1
unnamed: J9.4, R39.1
unnamed: J10.2, R44.1
unnamed: J10.3, R43.1
unnamed: J10.4, R42.1
unnamed: J12.3, R49.1
unnamed: J13.2, R51.1
unnamed: J14.2, R52.1
unnamed: J15.3, R53.2
unnamed: J16.3, R62.1
unnamed: J17.2, R57.1
unnamed: J17.3, R56.1
unnamed: J17.4, R55.1
unnamed: J17.5, R54.1
unnamed: J18.2, R61.1
unnamed: J18.3, R60.1
unnamed: J18.4, R59.1
unnamed: J18.5, R58.1
unnamed: J19.2, R63.2, U13.6 (CANL)
unnamed: J19.3, R63.1, U13.7 (CANH)
unnamed: J20.2, R69.1
unnamed: J20.3, R68.1
unnamed: J21.2, R71.1
unnamed: J21.3, R70.1
unnamed: J22.2, R73.1
unnamed: J22.3, R72.1
unnamed: J23.3, R65.1
unnamed: P1.2 (D-), R27.1
unnamed: P1.3 (D+), R28.1
unnamed: Q1.4 (S), U1.1 (IN1), U1.2 (IN1), U1.3 (EN1)
unnamed: Q2.1 (G), R45.1, R46.1
unnamed: R1.1, U3.69 (PA10)
unnamed: R2.2, U3.41 (PE10)
unnamed: R4.1, U3.43 (PE12)
unnamed: R5.1, U1.4 (Clim1)
unnamed: R6.1, U1.5 (Clim2)
unnamed: R13.1, U3.37 (PB2)
unnamed: R14.2, U3.94 (BOOT0)
unnamed: R31.1, U11.12 (PA2)
unnamed: R32.1, U11.13 (PA3)
unnamed: R33.1, U11.38 (PA15)
unnamed: R48.2, U11.20 (PB2)
unnamed: R64.2, R65.2, U14.3 (2Y)

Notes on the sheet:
IMU
IO CHANNELS
CAN
http://www.nxp.com/documents/data_sheet/74LVC2G86.pdf
TODO: Testpoint
SPARE ADC
AUAV X2.1 http://autode.sk/2BT1NOc
https://github.com/mRoboticsIO/Hardware/blob/master/X2.1/Docs/mRo_X21_r2_drawings.pdf
TODO: CHECK VDD_SERVO_SENS
TODO: CHECK IO_POWER_BREATHING
HARDWARE BIT Pixhawk 1: PC14 Floating PC15 Floating Pixhawk 2: PC14 3.3v PC15 GND
https://github.com/PX4/Firmware/blob/master/src/drivers/boards/auav-x21/board_config.h
STM32F7x5
https://goo.gl/fLnw3r
DORCA-30 SPI SPI_EXT
SBUS INPUT
SPEKTRUM SATELLITE
SERIAL
POWER
FMU
OTHER PORTS
POWER IN
MPU9250 PCB Guide https://store.invensense.com/datasheets/invensense/Accelerometer_Gyroscope_Design_Guidelines.pdf
BATT_VOLT_SENS, BATT_CURR_SENS 순서 바뀜. IC20608 DRY, CS 라인 바뀜

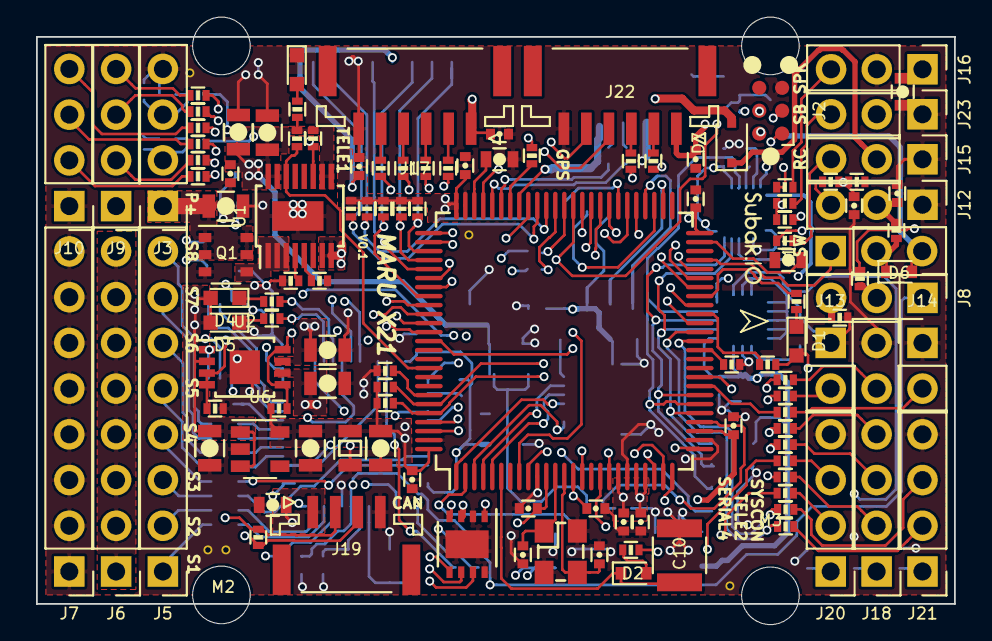
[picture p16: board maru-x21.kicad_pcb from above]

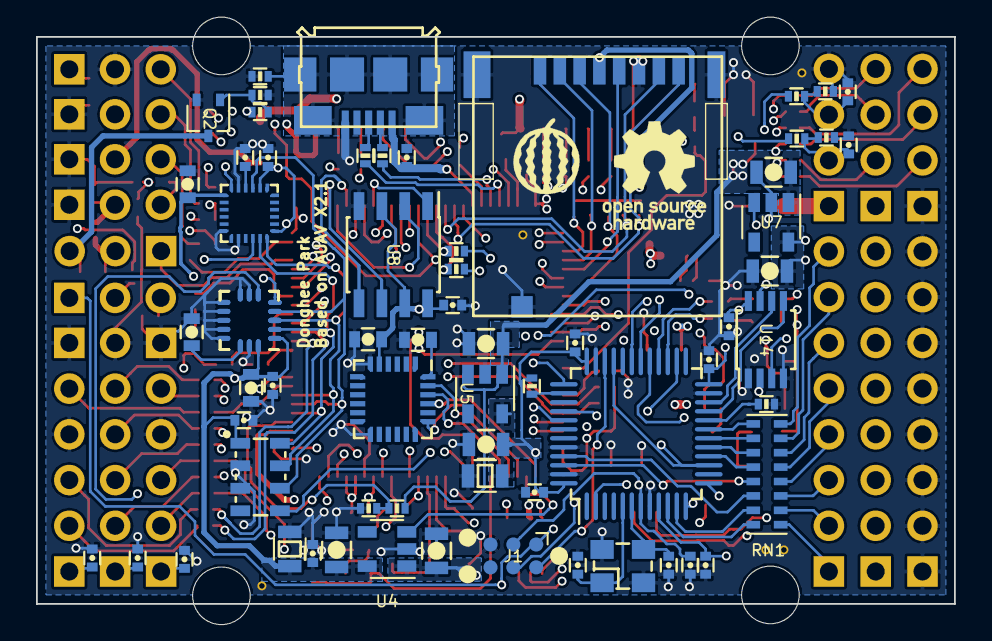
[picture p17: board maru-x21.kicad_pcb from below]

Board: 4 copper layers, 51.0 x 31.5 mm, 189 parts (66 on the bottom side), 174 nets.

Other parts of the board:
U12#2: ICM-20602; LGA-16_3x3mm_Pitch0.5mm

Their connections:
/20608_CS: U12#2.6; also elsewhere on the board
/20608_DRDY: U12#2.5; also elsewhere on the board
/SPI_INT_MISO: U12#2.4; also elsewhere on the board
/SPI_INT_MOSI: U12#2.3; also elsewhere on the board
/SPI_INT_SCK: U12#2.2; also elsewhere on the board
/VDD_3V3_SENSORS: U12#2.1, U12#2.16; also elsewhere on the board
GND: U12#2.7, U12#2.8, U12#2.9, U12#2.10, U12#2.11, U12#2.12, U12#2.13, U12#2.15; also elsewhere on the board
unnamed 110: U12#2.14; also elsewhere on the board

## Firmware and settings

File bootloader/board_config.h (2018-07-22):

/****************************************************************************
 *
 *   Copyright (c) 2013-2016 PX4 Development Team. All rights reserved.
 *
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
 * 1. Redistributions of source code must retain the above copyright
 *    notice, this list of conditions and the following disclaimer.
 * 2. Redistributions in binary form must reproduce the above copyright
 *    notice, this list of conditions and the following disclaimer in
 *    the documentation and/or other materials provided with the
 *    distribution.
 * 3. Neither the name PX4 nor the names of its contributors may be
 *    used to endorse or promote products derived from this software
 *    without specific prior written permission.
 *
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
 ****************************************************************************/

/**
 * @file board_config.h
 *
 * MARU X2.1 internal definitions
 */

#pragma once

/****************************************************************************************************
 * Included Files
 ****************************************************************************************************/

#include <px4_config.h>
#include <nuttx/compiler.h>
#include <stdint.h>

/****************************************************************************************************
 * Definitions
 ****************************************************************************************************/
/* Configuration ************************************************************************************/

/* PX4IO connection configuration */
#define BOARD_USES_PX4IO_VERSION       2
#define PX4IO_SERIAL_DEVICE	"/dev/ttyS4"
#define PX4IO_SERIAL_TX_GPIO	GPIO_USART6_TX
#define PX4IO_SERIAL_RX_GPIO	GPIO_USART6_RX
#define PX4IO_SERIAL_BASE	STM32_USART6_BASE	/* hardwired on the board */
#define PX4IO_SERIAL_VECTOR	STM32_IRQ_USART6
#define PX4IO_SERIAL_TX_DMAMAP	DMAMAP_USART6_TX_2
#define PX4IO_SERIAL_RX_DMAMAP	DMAMAP_USART6_RX_2
#define PX4IO_SERIAL_RCC_REG	STM32_RCC_APB2ENR
#define PX4IO_SERIAL_RCC_EN	RCC_APB2ENR_USART6EN
#define PX4IO_SERIAL_CLOCK	STM32_PCLK2_FREQUENCY
#define PX4IO_SERIAL_BITRATE	1500000			/* 1.5Mbps -> max rate for IO */


/* PX4FMU GPIOs ***********************************************************************************/
/* LEDs */

#define GPIO_LED1		(GPIO_OUTPUT|GPIO_OPENDRAIN|GPIO_SPEED_50MHz|GPIO_OUTPUT_CLEAR|GPIO_PORTE|GPIO_PIN12)

/* External interrupts but on board*/
#define GPIO_EXTI_MPU_DRDY              (GPIO_INPUT|GPIO_FLOAT|GPIO_EXTI|GPIO_PORTD|GPIO_PIN15)

/* Data ready pins but on board */

//#define GPIO_EXTI_ICM_2060X_DRDY      (GPIO_INPUT|GPIO_FLOAT|GPIO_EXTI|GPIO_PORTC|GPIO_PIN14)
// MARU X21
#define GPIO_EXTI_ICM_2060X_DRDY      (GPIO_INPUT|GPIO_FLOAT|GPIO_EXTI|GPIO_PORTC|GPIO_PIN15)

/* Data ready pins off */
#define GPIO_EXTI_MPU_DRDY_OFF          (GPIO_INPUT|GPIO_PULLDOWN|GPIO_EXTI|GPIO_PORTD|GPIO_PIN15)
//#define GPIO_EXTI_ICM_2060X_DRDY_OFF  (GPIO_INPUT|GPIO_PULLDOWN|GPIO_EXTI|GPIO_PORTC|GPIO_PIN14)
// MARU X21
#define GPIO_EXTI_ICM_2060X_DRDY_OFF  (GPIO_INPUT|GPIO_PULLDOWN|GPIO_EXTI|GPIO_PORTC|GPIO_PIN15)

/* SPI1 off */
#define GPIO_SPI1_SCK_OFF   (GPIO_INPUT|GPIO_PULLDOWN|GPIO_PORTA|GPIO_PIN5)
#define GPIO_SPI1_MISO_OFF  (GPIO_INPUT|GPIO_PULLDOWN|GPIO_PORTA|GPIO_PIN6)
#define GPIO_SPI1_MOSI_OFF  (GPIO_INPUT|GPIO_PULLDOWN|GPIO_PORTA|GPIO_PIN7)

/* SPI1 chip selects off */
//#define GPIO_SPI_CS_ICM_2060X_OFF (GPIO_INPUT|GPIO_PULLDOWN|GPIO_SPEED_2MHz|GPIO_PORTC|GPIO_PIN15)
// MARU X21
#define GPIO_SPI_CS_ICM_2060X_OFF (GPIO_INPUT|GPIO_PULLDOWN|GPIO_SPEED_2MHz|GPIO_PORTC|GPIO_PIN14)
#define GPIO_SPI_CS_BARO_OFF        (GPIO_INPUT|GPIO_PULLDOWN|GPIO_SPEED_2MHz|GPIO_PORTD|GPIO_PIN7)
#define GPIO_SPI_CS_MPU_OFF		    (GPIO_INPUT|GPIO_PULLDOWN|GPIO_SPEED_2MHz|GPIO_PORTC|GPIO_PIN2)

/* SPI chip selects */
//#define GPIO_SPI_CS_ICM_2060X	 (GPIO_OUTPUT|GPIO_PUSHPULL|GPIO_SPEED_2MHz|GPIO_OUTPUT_SET|GPIO_PORTC|GPIO_PIN15)
// MARU X21
#define GPIO_SPI_CS_ICM_2060X	 (GPIO_OUTPUT|GPIO_PUSHPULL|GPIO_SPEED_2MHz|GPIO_OUTPUT_SET|GPIO_PORTC|GPIO_PIN14)
#define GPIO_SPI_CS_BARO         (GPIO_OUTPUT|GPIO_PUSHPULL|GPIO_SPEED_2MHz|GPIO_OUTPUT_SET|GPIO_PORTD|GPIO_PIN7)
#define GPIO_SPI_CS_FRAM         (GPIO_OUTPUT|GPIO_PUSHPULL|GPIO_SPEED_2MHz|GPIO_OUTPUT_SET|GPIO_PORTD|GPIO_PIN10)
#define GPIO_SPI_CS_MPU          (GPIO_OUTPUT|GPIO_PUSHPULL|GPIO_SPEED_2MHz|GPIO_OUTPUT_SET|GPIO_PORTC|GPIO_PIN2)

#define PX4_SPI_BUS_SENSORS	1
#define PX4_SPI_BUS_RAMTRON	2
#define PX4_SPI_BUS_BARO	PX4_SPI_BUS_SENSORS

/* Use these in place of the uint32_t enumeration to select a specific SPI device on SPI1 */
#define PX4_SPIDEV_ICM_20602 PX4_MK_SPI_SEL(PX4_SPI_BUS_SENSORS, 1)
#define PX4_SPIDEV_ICM_20608 PX4_MK_SPI_SEL(PX4_SPI_BUS_SENSORS, 2)
#define PX4_SPIDEV_BARO      PX4_MK_SPI_SEL(PX4_SPI_BUS_SENSORS, 3)
#define PX4_SPIDEV_MPU       PX4_MK_SPI_SEL(PX4_SPI_BUS_SENSORS, 4)

/* I2C busses */

/* There is no I2C2 so there is not notion of internal / external*/
#define PX4_I2C_BUS_EXPANSION 1
#define PX4_I2C_BUS_LED		PX4_I2C_BUS_EXPANSION
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

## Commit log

2018-07-22 Add schematic and board, bom files
    [maru-pixracer-B.Cu.gbr, maru-pixracer-B.Mask.gbr, maru-pixracer-B.Paste.gbr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]
2018-07-22 Add PCB pdf file
2018-07-22 Add Case STL file
    [maru-x21-bottom-case.stl, maru-x21-top-case.stl]
2018-07-22 Add PX4 board_config.h
2018-07-22 Add assembly and madien flight video
2019-11-20 Add Interactive BOM builder
2020-02-26 Added interactive html bom
2020-07-14 Add bom

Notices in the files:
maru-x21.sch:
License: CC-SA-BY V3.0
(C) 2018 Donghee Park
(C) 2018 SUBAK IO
